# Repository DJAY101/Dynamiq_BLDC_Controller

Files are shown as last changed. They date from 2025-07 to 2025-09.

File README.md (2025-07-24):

# A simple Brushless Motor Controller
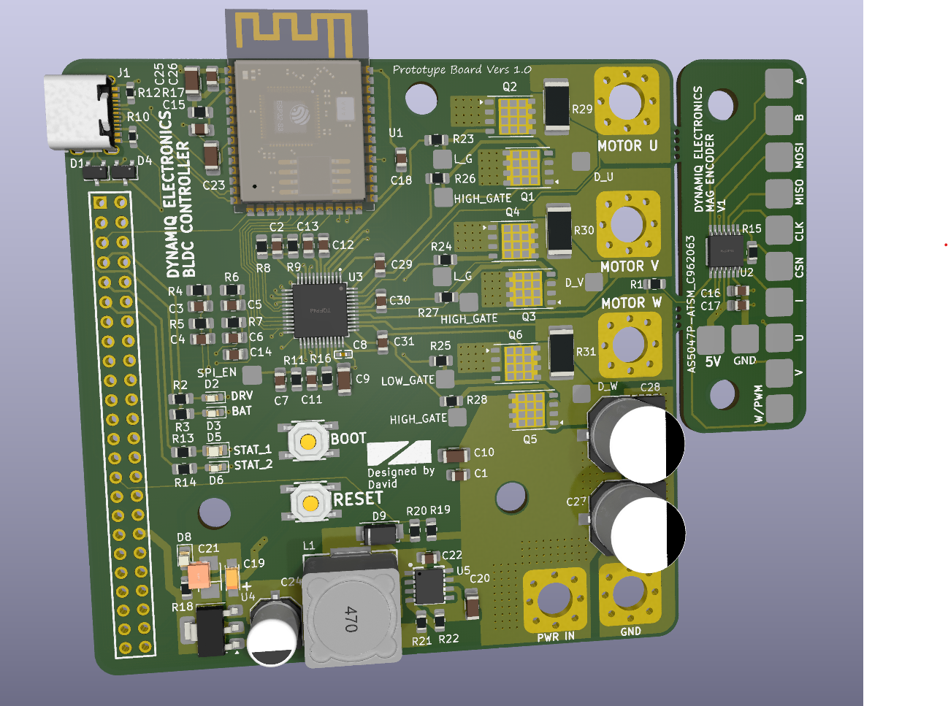
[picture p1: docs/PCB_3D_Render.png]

I'm currently on the journey of creating a simple cost effective controller that
will eventually be sold to the masses to remove the high barrier to entry into using high performing brushless motor actuators.

FRC Falcon 500 Motors inspired this project, since there are no suitable motor options at a suitable price that enables hobbyists to utilise these amazing pieces of technology. (Odrive being 200USD+)

# This project is still in its very early stages...
(Do note this is actually my very second PCB designed, so I lack a lot of experience)

Version 1 of the PCB worked with the following code. However I ended up frying two of the boards during programming and tinkering with the board. I am currently working on a version 2 iteration of the PCB from the mistakes and lack of safety features in V1. 

(I actually got the motor to turn on the very first iteration of this board which is a massive win)

## Failures so far...
- Somehow killed the TMC6200 gate driver while I was tinkering with the code. it does not like being fed a PWM duty cycle of greater than 40%
- Magic smoke occured on my buck converter where 4s Lipo is converted to 5V. Still unsure what happened here, but I have a few hypothesis. Sketchy soldering on my ESP32 3.3v and ground pin causing a short. Or accidentally shorting the the SPI clock pin with ground while unplugging the jumpers.
- The board does heat up, perhaps 2oZ layers may be needed (opted out since it was expensive for iter1)
- Practically no protection circuitry at all, except for the built in ones in the gate driver

# Improvements Underway
The progress on the code is halted as I have no working boards anymore since I fried all 2 of them haha.
- Integrate reverse polarity protection with a MOSFET Diode*
- Remove the chunky header pin and replace it with smaller header pins that connect to encoders and etc
- Initial inrush current limit to stop the spark when I connect my lipo to the board
- Fuses... Fuses and more fuses
- Change my LDO to a newer IC for more efficiency
- Capacitors on the phase output?
- Current sensing was not tested before the boards fried themselves ( caps on current sens outputs for a better averages value?)

# Other Unstructured Yap
PCB was manufactured by JLPCB, assembly services was also opted, 5 boards were 10 bucks aud and assembly and parts for 2 board added $150 aud

Reddit also reviewd my board before I manufactured it heres the link to that discussion
https://www.reddit.com/r/PCB/comments/1lk1n3d/review_request_my_first_pcb_bldc_sinusoidal/

This man made coding this thing a lot easier. Just pass sine waves into the motor and itll turn. I reckon it was much more easier to implement than step control.
https://www.youtube.com/watch?v=zSdetJsSeNw&t

Cool channels
- https://www.youtube.com/watch?v=mbJOxqxLkLE
- https://www.youtube.com/watch?v=e0sQnVmE7DU

If you'd like to contact me for more information or collaboration on this project feel free to DM me on insta at DJAY10101, or if you prefer email its djay01602@gmail.com

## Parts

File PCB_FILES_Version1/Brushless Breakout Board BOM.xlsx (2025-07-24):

Comment | Designator | Footprint | JLCPCB Part #（optional）
N-MOSFETS | Q1, Q2, Q3, Q4, Q5, Q6 | PG-TDSON-8 | C3288901
Buttons | SW1, SW2 | SW-SMD_4P-L5.2-W5.2-P3.70-LS6.5 | C10852
Mosfet Driver | U3 | TQFP-48_L7.0-W7.0-P0.50-LS9.0-BL-EP | C465958
ESP-32 MCU | U1 | SMD,18x25.5mm | C2913199
Jumper Connector | H1 | HC-PM254-8.5H-2X24PZ | C27985239
Mag Encoder | U2 | TSSOP-14 | C962063
Buck Convert IC | U5 | ESOP-8_L4.9-W3.9-P1.27-LS6.0-TL-EP | C9864
LDO IC | U4 | SOT-223 | C347222
ESD Protect IC | D1, D4 | SOT-23-3_L3.0-W1.7-P0.95-LS2.9-BR | C32677
USB C | J1 | TYPE-C-31-M-12 | C165948
Green LED | D8 | D0805 | C2297
LED Resistor 150R | R18, R2, R3, R13, R14 | R0805 | C17471
Red LED | D2, D3, D6 | D0603 | C2286
Yellow LED | D5 | D0805 | C2296
USB Resistor 5.1K | R10, R12 | R0603 | C23186
10K | R1, R4, R5, R6, R7, R8, R9, R11, R15, R17, R19, R21 | R0805 | C17414
10mR Shun Resistor | R29, R30, R31 | R2512 | C241862
2.2R Gate Resistors | R23, R24, R25, R26, R27, R28 | R0805 | C17521
47R | R16 | R0805 | C17714
1K | R20 | R0805 | C17513
3.3K | R22 | R0805 | C26010
15uH Buck Conv Inductor | L1 | IND-SMD_L12.5-W12.5_RLF12545T | C40000
SS34 Diode | D9 | SMA(DO-214AC) | C8678
100nF 100V Caps | C1, C2, C3, C4, C5, C6, C7, C14, C15, C17, C18, C26 | C0805 | C28233
100nF 50V Caps | C9, C10 | C1206 | C24497
100nf 16V Caps | C8 | C0402 | C1525
22nF 100V | C11 | C0805 | C184772
10uF 50V Caps | C20, C25 | C1206 | C13585
2.2uF 50V Caps | C13 | C0805 | C377773
4.7uF 25V | C12 | C0805 | C1779
1uF 50V | C16 | C0805 | C28323
22uF 10V Tantalum | C21 | CASE-B-3528-21(mm) | C7198
10nF 50V | C22 | C0805 | C1710
100uF 6.3V | C23 | C1206 | C15008
470uF | C27, C28 | CAP-SMD_BD10.0-L10.3-W10.3-LS11.3-FD | C3351
470nF 50V | C29, C30, C31 | C0805 | C13967
10uF 16V Tantalum | C19 | CASE-A-3216-18(mm) | C7171
220 uF capacitor | C24 | CAP-SMD_BD6.3-L6.6-W6.6-FD | C3342

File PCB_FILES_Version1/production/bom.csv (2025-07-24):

Designator | Footprint | Quantity | Value | LCSC Part #
C1, C14, C2 | 0805 | 3 | 100nF
C10, C9 | 1206 | 2 | 100nF 50V
C11 | 0805 | 1 | 22nF 100V
C12 | 0805 | 1 | 4.7uF
C13 | 0805 | 1 | 2.2uF
C15, C17, C18, C26, C3, C4, C5, C6, C7 | 0805 | 9 | 0.1uF
C16 | 0805 | 1 | 1uF
C19 | CAP-SMD_L3.2-W1.6-RD-C7171 | 1 | 10uF - TAJA106K016RNJ | C7171
C20, C25 | 1206 | 2 | 10uF
C21 | CAP-SMD_L3.5-W2.8-R-RD | 1 | 22uF Tant TAJB226K010RNJ | C7198
C22 | 0805 | 1 | 0.01uF
C23 | 1206 | 1 | 100uF
C24 | CAP-SMD_BD6.3-L6.6-W6.6-FD | 1 | 220uF-C3342 | C3342
C27, C28 | CAP-SMD_BD10.0-L10.3-W10.3-LS11.3-FD | 2 | 470uF -C3351 | C3351
C29, C30, C31 | 0805 | 3 | 470nF 16V
C8 | C0402 | 1 | 100nF 16V
D1, D4 | SOT-23-3_L3.0-W1.7-P0.95-LS2.9-BR | 2 | PSM712-LF-T7 | C32677
D2 | 0603 | 1 | Fault_LED
D3 | 0603 | 1 | LIPO_ALERT
D5 | 0805 | 1 | STATUS_1_LED
D6 | 0603 | 1 | STATUS_2_LED
D8 | 0805 | 1 | LED
D9 | SMA_L4.3-W2.6-LS5.2-RD | 1 | SS34
GND | PWR_THRU_HOLE | 1 | BAT_GND
H1 | HDR-TH_48P-P2.54-V-F-R2-C24-S2.54 | 1 | HC-PM254-8.5H-2X24PZ | C27985239
J1 | USB-C_SMD-TYPE-C-31-M-12 | 1 | USB_C_Receptacle_USB2.0_16P
L1 | IND-SMD_L12.5-W12.5_RLF12545T | 1 | 15uH
MOTOR U | PWR_THRU_HOLE | 1 | Motor_Phase_U
MOTOR V | PWR_THRU_HOLE | 1 | Motor_Phase_V
MOTOR W | PWR_THRU_HOLE | 1 | Motor_Phase_W
PWR IN | PWR_THRU_HOLE | 1 | BAT_IN
Q1, Q2, Q3, Q4, Q5, Q6 | Infineon_PG-TDSON-8_6.15x5.15mm | 6 | N_FET_ISC0602NLS
R1, R11, R15, R17, R19, R21, R4, R5, R6, R7, R8, R9 | 0805 | 12 | 10K
R10, R12 | 0603 | 2 | 5.1K
R13, R14, R18, R2, R3 | 0805 | 5 | 150
R16 | 0805 | 1 | 47
R20 | 0805 | 1 | 1K
R22 | 0805 | 1 | 3.3K
R23, R24, R25, R26, R27, R28 | 0805 | 6 | 2.2
R29, R30, R31 | 2512 | 3 | 10mR
SW1, SW2 | SW-SMD_4P-L5.2-W5.2-P3.70-LS6.5 | 2 | SW_MEC_5E
TP1 | PAD_TP | 1 | SPI_EN
TP10 | Small_Pad_4mm | 1 | 5V_ENCODER
TP11 | Small_Pad_4mm | 1 | U_ENCODER
TP12 | Small_Pad_4mm | 1 | V_ENCODER
TP13 | Small_Pad_4mm | 1 | W/PWM_ENCODER
TP19, TP20 | PAD_TP | 2 | L_G
TP2 | Small_Pad_4mm | 1 | CSN_ENCODER
TP21 | PAD_TP | 1 | LOW_GATE
TP22, TP23, TP24 | PAD_TP | 3 | HIGH_GATE
TP25 | PAD_TP | 1 | D_U
TP26 | PAD_TP | 1 | D_V
TP27 | PAD_TP | 1 | D_W
TP3 | Small_Pad_4mm | 1 | CLK_ENCODER
TP4 | Small_Pad_4mm | 1 | MISO_ENCODER
TP5 | Small_Pad_4mm | 1 | MOSI_ENCODER
TP6 | Small_Pad_4mm | 1 | GND_ENCODER
TP7 | Small_Pad_4mm | 1 | B_ENCODER
TP8 | Small_Pad_4mm | 1 | A_ENCODER
TP9 | Small_Pad_4mm | 1 | I_ENCODER
U1 | ESP32-S3-WROOM-1 | 1 | ESP32-S3-WROOM-1
U2 | TSSOP-14_L5.0-W4.4-P0.65-LS6.4-BL | 1 | AS5047P-ATSM_C962063 | C962063
U3 | TQFP-48_L7.0-W7.0-P0.50-LS9.0-BL-EP | 1 | TMC6200-TA-T | C465958
U4 | SOT-223-3_TabPin2 | 1 | AMS1117-3.3
U5 | ESOP-8_L4.9-W3.9-P1.27-LS6.0-TL-EP | 1 | TPS5430DDAR | C9864

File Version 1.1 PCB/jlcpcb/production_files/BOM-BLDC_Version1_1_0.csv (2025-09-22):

Comment | Designator | Footprint | LCSC | Quantity
SW_MEC_5E | SW1,SW2 | SW-SMD_4P-L5.2-W5.2-P3.70-LS6.5 | C10852 | 2
SM06B-GHS-TB(LF)(SN) | CN3 | CONN-TH_SM06B-GHS-TB-LF-SN | C133065 | 1
470nF 16V | C13,C14,C29 | C_0805_2012Metric_Pad1.18x1.45mm_HandSolder | C13967 | 3
100uF | C6,C9 | C_0805_2012Metric_Pad1.18x1.45mm_HandSolder | C141660 | 2
10uF | C1,C3,C7 | C_0805_2012Metric_Pad1.18x1.45mm_HandSolder | C15850 | 3
USB_C_Receptacle_USB2.0_14P | J1 | USB-C_SMD-TYPE-C-31-M-12 | C165948 | 1
0.01uF | C8 | C_0805_2012Metric_Pad1.18x1.45mm_HandSolder | C1710 | 1
10K | R10,R17,R19,R20,R21,R22,R24,R25,R27,R5,R8 | R_0805_2012Metric_Pad1.20x1.40mm_HandSolder | C17414 | 11
150 | R1,R2,R3,R4,R7 | R_0805_2012Metric_Pad1.20x1.40mm_HandSolder | C17471 | 5
1K | R6 | R_0805_2012Metric_Pad1.20x1.40mm_HandSolder | C17513 | 1
2.2 | R12,R13,R15,R16,R23,R26 | R_0805_2012Metric_Pad1.20x1.40mm_HandSolder | C17521 | 6
47 | R28 | R_0805_2012Metric_Pad1.20x1.40mm_HandSolder | C17714 | 1
4.7uF | C20,C4,C5 | C_0805_2012Metric_Pad1.18x1.45mm_HandSolder | C1779 | 3
LED | D1,D2 | LED_0603_1608Metric_Pad1.05x0.95mm_HandSolder | C2286 | 2
LED | D3 | LED_0805_2012Metric_Pad1.15x1.40mm_HandSolder | C2296 | 1
LED | D4,D6 | LED_0805_2012Metric_Pad1.15x1.40mm_HandSolder | C2297 | 2
3.3K | R11,R9 | R_0805_2012Metric_Pad1.20x1.40mm_HandSolder | C26010 | 2
0.1uF | C15,C17,C18,C2,C22,C23,C25,C26,C27 | C_0805_2012Metric_Pad1.18x1.45mm_HandSolder | C28233 | 9
2.2uF | C21 | C_0805_2012Metric_Pad1.18x1.45mm_HandSolder | C377773 | 1
DB910-7.62-3P | CN1 | CONN-TH_3P-P7.62_DB910-7.62-3P | C395877 | 1
SRV05-4-HXY | U10,U11,U13,U14 | SOT-23-6_L2.9-W1.6-P0.95-LS2.8-BR | C4748793 | 4
SM03B-GHS-TB(LF)(SN) | CN4 | CONN-TH_SM03B-GHS-TB-LF-SN | C514175 | 1
TestPoint | TP14,TP15,TP16,TP19,TP2,TP22,TP25,TP3,TP4,TP5,TP6,TP7 | SMD_RH-5015 | C5199798 | 12
22nF 100V | C28 | C_0805_2012Metric_Pad1.18x1.45mm_HandSolder | C61998 | 1
USBLC6-2SC6 | D9 | SOT-23-6_L2.9-W1.6-P0.95-LS2.8-BL | C7519 | 1
TPS5430DDAR | U4 | ESOP-8_L4.9-W3.9-P1.27-LS6.0-TL-EP | C9864 | 1
XT60PW-M | CN2 | CONN-TH_XT60PW-M | C98732 | 1

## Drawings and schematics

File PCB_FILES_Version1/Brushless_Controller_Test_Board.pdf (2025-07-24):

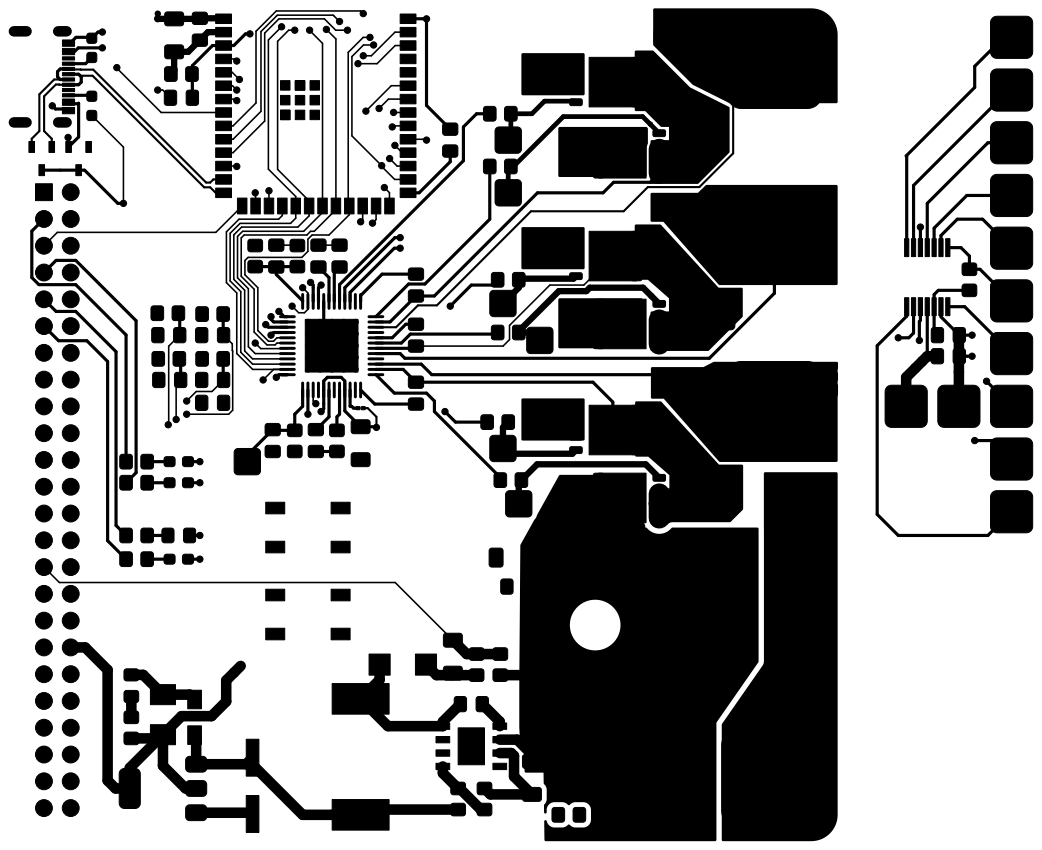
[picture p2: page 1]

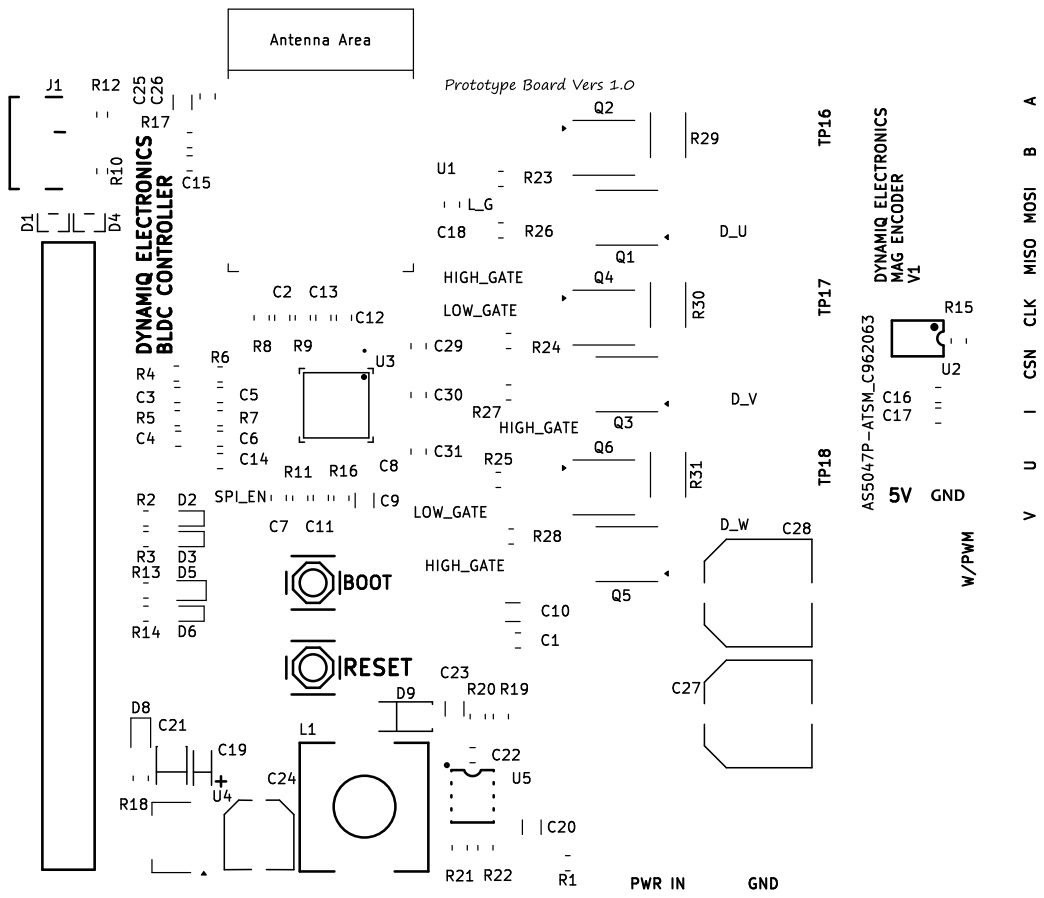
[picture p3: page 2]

B DYNAMIQ ELECTRONICS MAG ENCODER V1 CSN W/PWM

I DYNAMIQ ELECTRONICS BLDC CONTROLLER

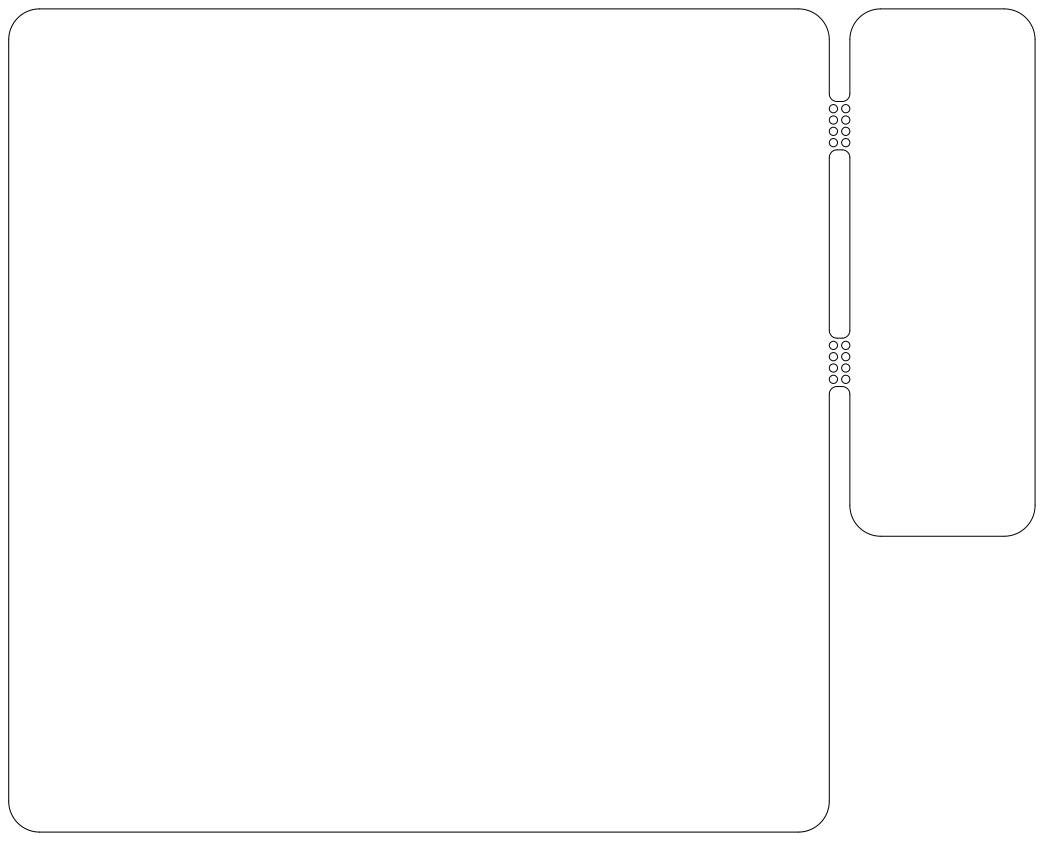
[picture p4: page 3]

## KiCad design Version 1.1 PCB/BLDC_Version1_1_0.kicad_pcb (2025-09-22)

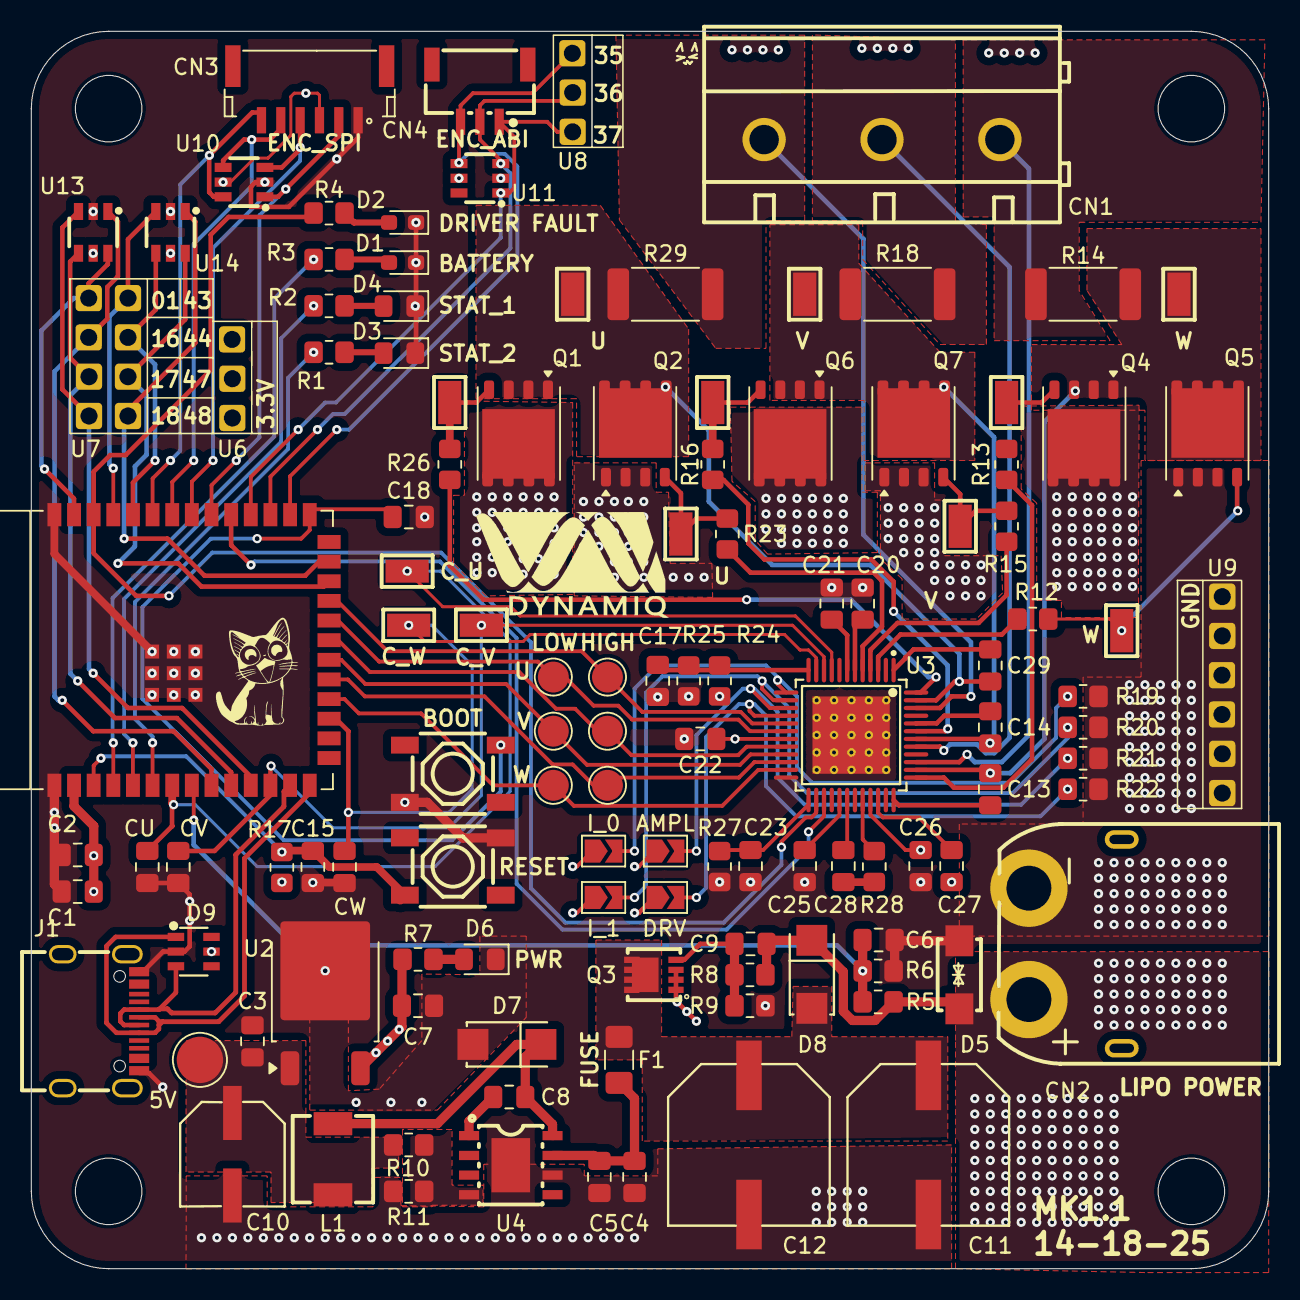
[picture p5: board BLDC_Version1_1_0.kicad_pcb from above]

Board: 4 copper layers, 80.0 x 80.0 mm, 118 parts (0 on the bottom side), 82 nets.

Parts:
5V: TestPoint; TestPoint_Pad_D3.0mm
AMPL: SolderJumper_2_Open; SolderJumper-2_P1.3mm_Open_TrianglePad1.0x1.5mm
C1, C3, C7: 10uF; C_0805_2012Metric_Pad1.18x1.45mm_HandSolder
C2, C15, C17, C18, C22, C23: 0.1uF; C_0805_2012Metric_Pad1.18x1.45mm_HandSolder
C4, C5, C20: 4.7uF; C_0805_2012Metric_Pad1.18x1.45mm_HandSolder
C6, C9: 100uF; C_0805_2012Metric_Pad1.18x1.45mm_HandSolder
C8: 0.01uF; C_0805_2012Metric_Pad1.18x1.45mm_HandSolder
C10: 220uF; CAP-SMD_BD6.3-L6.6-W6.6-FD
C11, C12: RVT1E471M1010-C3351; CAP-SMD_BD10.0-L10.3-W10.3-LS11.0-FD
C13, C14, C29: 470nF 16V; C_0805_2012Metric_Pad1.18x1.45mm_HandSolder
C21: 2.2uF; C_0805_2012Metric_Pad1.18x1.45mm_HandSolder
C25, C26: 0.1uF 50V; C_0805_2012Metric_Pad1.18x1.45mm_HandSolder
C27: 100nF 16V; C_0805_2012Metric_Pad1.18x1.45mm_HandSolder
C28: 22nF 100V; C_0805_2012Metric_Pad1.18x1.45mm_HandSolder
CN1: DB910-7.62-3P; CONN-TH_3P-P7.62_DB910-7.62-3P
CN2: XT60PW-M; CONN-TH_XT60PW-M
CN3: SM06B-GHS-TB(LF)(SN); CONN-TH_SM06B-GHS-TB-LF-SN
CN4: SM03B-GHS-TB(LF)(SN); CONN-TH_SM03B-GHS-TB-LF-SN
CU: C; C_0805_2012Metric_Pad1.18x1.45mm_HandSolder
CV: C; C_0805_2012Metric_Pad1.18x1.45mm_HandSolder
CW: C; C_0805_2012Metric_Pad1.18x1.45mm_HandSolder
D1, D2: LED; LED_0603_1608Metric_Pad1.05x0.95mm_HandSolder
D3, D4, D6: LED; LED_0805_2012Metric_Pad1.15x1.40mm_HandSolder
D5: SMAJ18CA_C908822; SMA_L4.4-W2.8-LS5.1-BI
D7, D8: B340A-E3/61T; SMA_L4.3-W2.6-LS5.2-RD
D9: USBLC6-2SC6; SOT-23-6_L2.9-W1.6-P0.95-LS2.8-BL
DRV: SolderJumper_2_Open; SolderJumper-2_P1.3mm_Open_TrianglePad1.0x1.5mm
F1: 1A Fuse; Fuse_1206_3216Metric_Pad1.42x1.75mm_HandSolder
I_0, I_1: SolderJumper_2_Open; SolderJumper-2_P1.3mm_Open_TrianglePad1.0x1.5mm
J1: USB_C_Receptacle_USB2.0_14P; USB-C_SMD-TYPE-C-31-M-12
L1: 22uH; IND-SMD_L5.5-W5.2
Q1, Q2, Q4, Q5, Q6, Q7: N_FET_ISC0602NLS; Infineon_PG-TDSON-8_6.15x5.15mm
Q3: SI7129DN-T1-GE3; POWERPAK-1212-8_L3.3-W3.3-P0.65-BL-EP
R1, R2, R3, R4, R7: 150; R_0805_2012Metric_Pad1.20x1.40mm_HandSolder
R5, R8, R10, R17, R19, R20, R21, R22, R24, R25, R27: 10K; R_0805_2012Metric_Pad1.20x1.40mm_HandSolder
R6: 1K; R_0805_2012Metric_Pad1.20x1.40mm_HandSolder
R9, R11: 3.3K; R_0805_2012Metric_Pad1.20x1.40mm_HandSolder
R12, R13, R15, R16, R23, R26: 2.2; R_0805_2012Metric_Pad1.20x1.40mm_HandSolder
R14, R18, R29: 10mR; R_2512_6332Metric_Pad1.40x3.35mm_HandSolder
R28: 47; R_0805_2012Metric_Pad1.20x1.40mm_HandSolder
SW1, SW2: SW_MEC_5E; SW-SMD_4P-L5.2-W5.2-P3.70-LS6.5
TP2, TP5, TP19: LOW_GATE; SMD_RH-5015
TP3, TP6, TP22: HIGH_GATE; SMD_RH-5015
TP4, TP7, TP25: OUTPUT_POINT; SMD_RH-5015
TP8, TP9, TP10, TP11, TP12, TP13: TestPoint; TestPoint_Pad_D2.0mm
TP14, TP15, TP16: TestPoint; SMD_RH-5015
U1: ESP32-S3-WROOM-1
U2: AP7363-33D-13; TO-252-2
U3: TMC6200-TA-T; TQFP-48_L7.0-W7.0-P0.50-LS9.0-BL-EP
U4: TPS5430DDAR; ESOP-8_L4.9-W3.9-P1.27-LS6.0-TL-EP
U6, U8: 1x3 Male Headers
U7: 8x Male Headers; 2x4 Male Headers
U9: Male Headers; 1x6 Male Headers
U10, U11, U13, U14: SRV05-4-HXY; SOT-23-6_L2.9-W1.6-P0.95-LS2.8-BR

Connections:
3.3V_BUS: AMPL.1 (A), C1.1, C2.1, C7.1, C22.1, CN3.3, D9.5, DRV.1 (A), I_0.1 (A), I_1.1 (A), R7.1, R17.1, R24.1, U1.2 (3V3), U2.3 (OUT), U3.19 (VCC_IO), U6.1, U6.2, U6.3, U10.5 (VBUS), U11.5 (VBUS), U13.5 (VBUS), U14.5 (VBUS)
5V_BUS: 5V.1, C3.1, C10.1, L1.2, R10.1, U2.1 (IN)
16.8V_BUS: C9.2, C25.1, C26.1, C27.1, CN2.2 (+), D5.2, D8.1 (K), Q1.5 (D), Q3.1 (S), Q3.2 (S), Q3.3 (S), Q4.5 (D), Q6.5 (D), R5.1, R8.1, U3.29 (VSA), U3.33 (VS)
/Power Management/SOFTSTART_PWR_IN: C11.1, C12.1, D8.2 (A), F1.1, Q3.5 (D), Q3.6 (D), Q3.7 (D), Q3.8 (D)
BOOT: C18.1, SW2.3 (K), U1.27 (GPIO0/BOOT)
CHARGE_CAPACITOR_INPUT: R28.2, U3.32 (CPI)
CHARGE_CAPACITOR_OUTPUT: C28.1, U3.30 (CPO)
CURRENT_SENS_VOFS: C17.1, R24.2, R25.1, U3.12 (VOFS/TEST)
CURRENT_U: CU.1, TP14.1, U1.7 (GPIO7/TOUCH7/ADC1_CH6), U3.9 (CURU)
CURRENT_V: CV.1, TP15.1, U1.12 (GPIO8/TOUCH8/ADC1_CH7/SUBSPICS1), U3.10 (CURV)
CURRENT_W: CW.1, TP16.1, U1.17 (GPIO9/TOUCH9/ADC1_CH8/FSPIHD/SUBSPIHD), U3.11 (CURW)
DRIVER_CSN/IDRV0: I_0.2 (B), R19.1, U3.13 (CSN_IDRV0)
DRIVER_SCK/IDRV1: I_1.2 (B), R20.1, U3.14 (SCK_IDRV1)
DRIVER_SDI/AMPL: AMPL.2 (B), R21.1, U3.15 (SDI_AMPLx10)
DRIVER_SDO/SINGLE: DRV.2 (B), R22.1, U3.16 (SDO_SINGLE)
DRIVER_U: C29.2, Q1.1 (S), Q1.2 (S), Q1.3 (S), Q2.5 (D), R29.1, TP25.1, U3.47 (U)
DRIVER_V: C14.2, Q6.1 (S), Q6.2 (S), Q6.3 (S), Q7.5 (D), R18.1, TP7.1, U3.42 (V)
DRIVER_W: C13.2, Q4.1 (S), Q4.2 (S), Q4.3 (S), Q5.5 (D), R14.1, TP4.1, U3.38 (W)
DRV_ENABLE: U1.31 (GPIO38/FSPIWP/SUBSPIWP), U3.27 (DEV_EN)
DRV_FAULT: R4.1, U1.38 (GPIO2/TOUCH2/ADC1_CH1), U3.26 (FAULT)
EN: C15.1, R17.2, SW1.3 (K), U1.3 (EN)
ENCODER_CLK: CN3.2, U1.32 (MTCK/GPIO39/CLK_OUT3/SUBSPICS1), U10.1
ENCODER_CSN: CN3.6, U1.35 (MTMS/GPIO42), U10.6
ENCODER_MISO: CN3.4, U1.33 (MTDO/GPIO40/CLK_OUT2), U10.3
ENCODER_MOSI: CN3.5, U1.34 (MTDI/GPIO41/CLK_OUT1), U10.4
GND: C1.2, C2.2, C3.2, C4.2, C5.2, C6.2, C7.2, C10.2, C11.2, C12.2, C15.2, C17.2, C18.2, C20.2, C21.2, C22.2, C23.2, C25.2, C26.2, CN2.1 (-), CN3.1, CU.2, CV.2, CW.2, D1.1 (K), D2.1 (K), D3.1 (K), D4.1 (K), D5.1, D6.1 (K), D7.2 (A), D9.2, J1.A1 (GND), J1.A12 (GND), J1.B1 (GND), J1.B12 (GND), Q2.1 (S), Q2.2 (S), Q2.3 (S), Q5.1 (S), Q5.2 (S), Q5.3 (S), Q7.1 (S), Q7.2 (S), Q7.3 (S), R6.2, R9.2, R11.2, R19.2, R20.2, R21.2, R22.2, R25.2, R27.2, SW1.2, SW2.2, U1.1 (GND), U1.40 (GND), U1.41 (GND), U2.2 (GND), U3.8 (GNDA), U3.24 (CLK), U3.49 (EP), U4.6 (GND), U4.9 (PowerPAD), U9.1, U9.2, U9.3, U9.4, U9.5, U9.6, U10.2 (GND), U11.2 (GND), U13.2 (GND), U14.2 (GND)
GPIO01: U1.39 (GPIO1/TOUCH1/ADC1_CH0), U7.1, U13.6
GPIO16: U1.9 (GPIO16/U0CTS/ADC2_CH5/XTAL_32K_N), U7.2, U13.1
GPIO17: U1.10 (GPIO17/U1TXD/ADC2_CH6), U7.3, U13.4
GPIO18: U1.11 (GPIO18/U1RXD/ADC2_CH7/CLK_OUT3), U7.4, U13.3
GPIO35: CN4.3, U1.28 (SPIIO6/GPIO35/FSPID/SUBSPID), U8.3, U11.4
GPIO36: CN4.2, U1.29 (SPIIO7/GPIO36/FSPICLK/SUBSPICLK), U8.2, U11.3
GPIO37: CN4.1, U1.30 (SPIDQS/GPIO37/FSPIQ/SUBSPIQ), U8.1, U11.1
GPIO43: U1.37 (U0TXD/GPIO43/CLK_OUT1), U7.5, U14.3
GPIO44: U1.36 (U0RXD/GPIO44/CLK_OUT2), U7.6, U14.4
GPIO47: U1.24 (GPIO47/SPICLK_P/SUBSPICLK_P_DIFF), U7.7, U14.6
GPIO48: U1.25 (GPIO48/SPICLK_N/SUBSPICLK_N_DIFF), U7.8, U14.1
LIPO_FAULT: R3.1, U1.4 (GPIO4/TOUCH4/ADC1_CH3)
LIPO_VOLT_SENS: C6.1, R5.2, R6.1, U1.8 (GPIO15/U0RTS/ADC2_CH4/XTAL_32K_P)
unnamed: C28.2, R28.1
unnamed: D1.2 (A), R3.2
unnamed: D2.2 (A), R4.2
unnamed: D3.2 (A), R1.2
unnamed: D4.2 (A), R2.2
unnamed: D6.2 (A), R7.2
unnamed: C8.2, D7.1 (K), L1.1, U4.8 (PH)
unnamed: Q1.4 (G), R26.2, TP22.1
unnamed: Q2.4 (G), R23.2, TP19.1
unnamed: C9.1, Q3.4 (G), R8.2, R9.1
unnamed: Q4.4 (G), R13.2, TP3.1
unnamed: Q5.4 (G), R12.2, TP2.1
unnamed: Q6.4 (G), R16.2, TP6.1
unnamed: Q7.4 (G), R15.2, TP5.1
unnamed: C21.1, U3.7 (5VOUT)
unnamed: C20.1, U3.6 (12VOUT)
unnamed: C23.1, R27.1, U3.25 (SPE)
unnamed: C8.1, U4.1 (BOOT)
unnamed: C4.1, C5.1, F1.2, U4.7 (VIN)
unnamed: R10.2, R11.1, U4.4 (VSENSE)
STATUS_1: R2.1, U1.5 (GPIO5/TOUCH5/ADC1_CH4)
STATUS_2: R1.1, U1.6 (GPIO6/TOUCH6/ADC1_CH5)
USB_D +: D9.1, J1.A6 (D+), J1.B6 (D+), U1.14 (GPIO20/U1CTS/ADC2_CH9/CLK_OUT1/USB_D+)
USB_D -: D9.3, J1.A7 (D-), J1.B7 (D-), U1.13 (GPIO19/U1RTS/ADC2_CH8/CLK_OUT2/USB_D-)
U_BOOTSTRAP: C29.1, U3.1 (CU)
U_HIGHSIDE: TP8.1, U1.23 (GPIO21), U3.17 (UH)
U_HIGHSIDE_GATE: R26.1, U3.48 (HSU)
U_LOWSIDE: TP9.1, U1.22 (GPIO14/TOUCH14/ADC2_CH3/FSPIWP/FSPIDQS/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), U3.18 (UL)
U_LOWSIDE_GATE: R23.1, U3.5 (LSU)
U_SENSE: CN1.3, R29.2, U3.46 (USENSE)
VOLTAGE_CHARGE_PUMP: C27.2, U3.34 (VCP)
V_BOOTSTRAP: C14.1, U3.44 (CV)
V_HIGHSIDE: TP10.1, U1.21 (GPIO13/TOUCH13/ADC2_CH2/FSPIQ/FSPIIO7/S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), U3.20 (VH)
V_HIGHSIDE_GATE: R16.1, U3.43 (HSV)
V_LOWSIDE: TP11.1, U1.20 (GPIO12/TOUCH12/ADC2_CH1/FSPICLK/FSPIIO6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), U3.21 (VL)
V_LOWSIDE_GATE: R15.1, U3.4 (LSV)
V_SENSE: CN1.2, R18.2, U3.41 (VSENSE)
W_BOOTSTRAP: C13.1, U3.36 (CW)
W_HIGHSIDE: TP12.1, U1.19 (GPIO11/TOUCH11/ADC2_CH0/FSPID/FSPIIO5/S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), U3.22 (WH)
W_HIGHSIDE_GATE: R13.1, U3.37 (HSW)
W_LOWSIDE: TP13.1, U1.18 (GPIO10/TOUCH10/ADC1_CH9/FSPICS0/FSPIIO4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), U3.23 (WL)
W_LOWSIDE_GATE: R12.1, U3.3 (LSW)
W_SENSE: CN1.1, R14.2, U3.39 (WSENSE)

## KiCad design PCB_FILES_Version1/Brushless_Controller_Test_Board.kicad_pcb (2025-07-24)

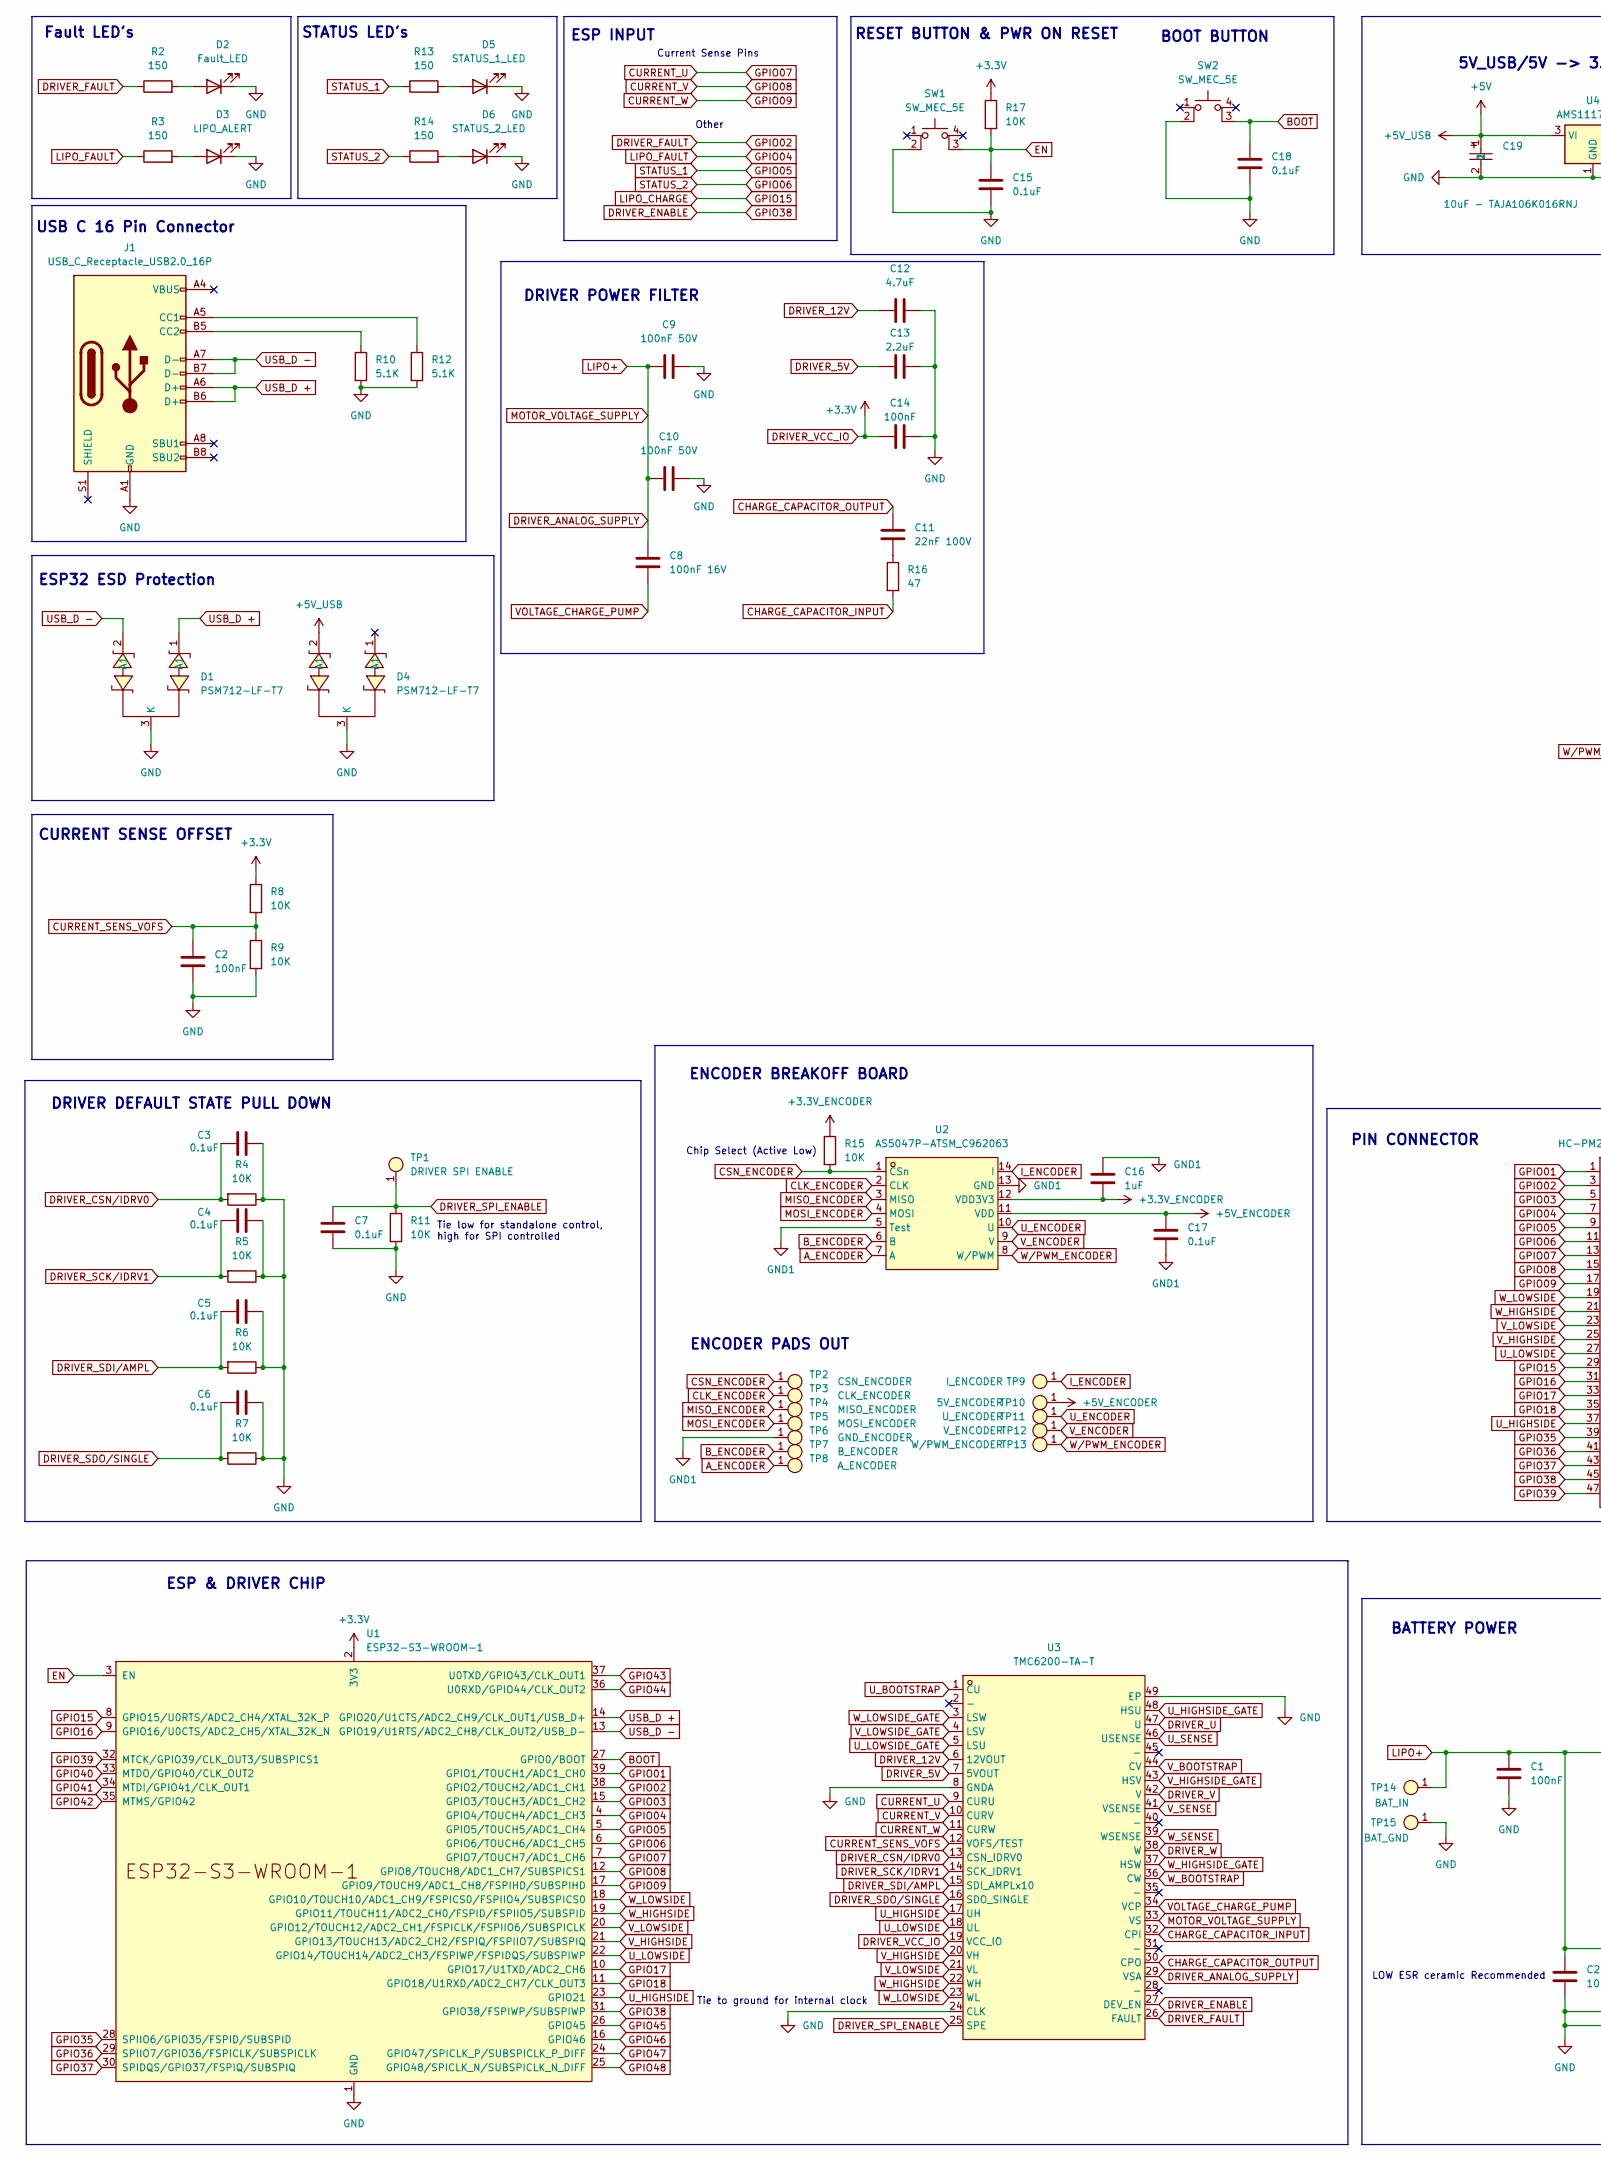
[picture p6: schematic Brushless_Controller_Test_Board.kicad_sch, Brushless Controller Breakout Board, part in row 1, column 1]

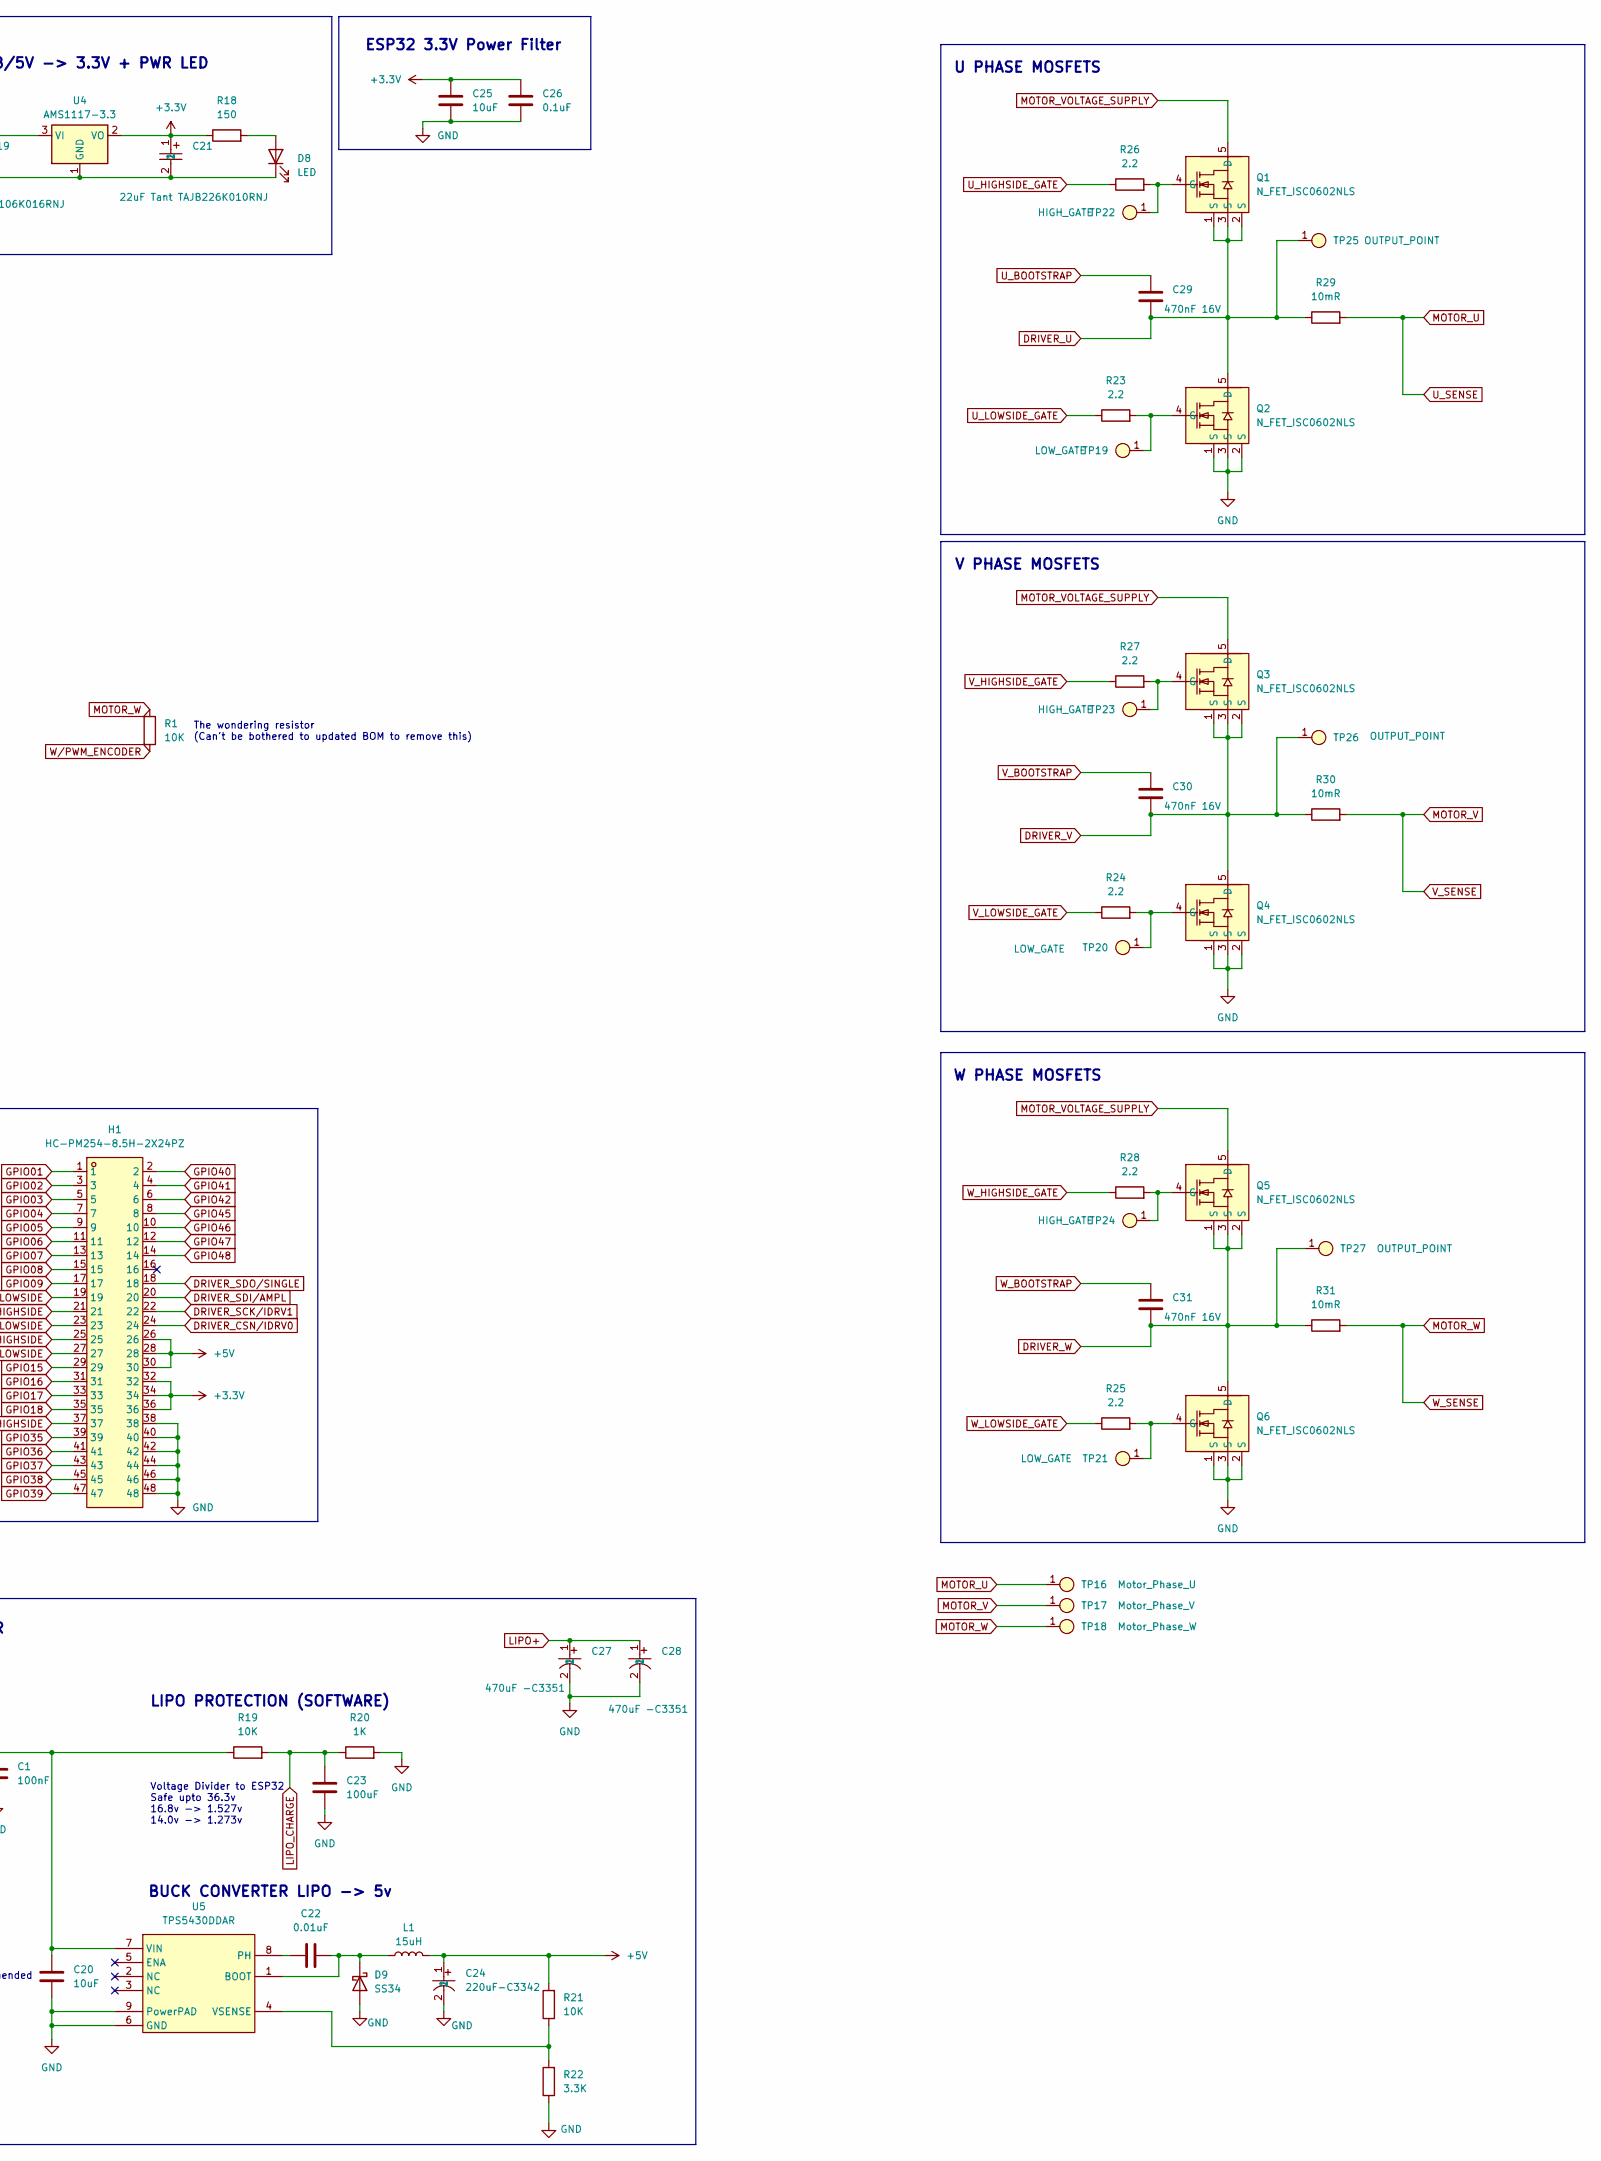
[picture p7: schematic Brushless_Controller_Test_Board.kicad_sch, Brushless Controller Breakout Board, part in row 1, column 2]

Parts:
C1, C2, C14: 100nF; C_0805_2012Metric_Pad1.18x1.45mm_HandSolder
C3, C4, C5, C6, C7, C15, C17, C18, C26: 0.1uF; C_0805_2012Metric_Pad1.18x1.45mm_HandSolder
C8: 100nF 16V; C_01005_0402Metric_Pad0.57x0.30mm_HandSolder
C9, C10: 100nF 50V; C_1206_3216Metric_Pad1.33x1.80mm_HandSolder
C11: 22nF 100V; C_0805_2012Metric_Pad1.18x1.45mm_HandSolder
C12: 4.7uF; C_0805_2012Metric_Pad1.18x1.45mm_HandSolder
C13: 2.2uF; C_0805_2012Metric_Pad1.18x1.45mm_HandSolder
C16: 1uF; C_0805_2012Metric_Pad1.18x1.45mm_HandSolder
C19: 10uF - TAJA106K016RNJ; CAP-SMD_L3.2-W1.6-RD-C7171; LCSC Part C7171
C20, C25: 10uF; C_1206_3216Metric_Pad1.33x1.80mm_HandSolder
C21: 22uF Tant TAJB226K010RNJ; CAP-SMD_L3.5-W2.8-R-RD; LCSC Part C7198
C22: 0.01uF; C_0805_2012Metric_Pad1.18x1.45mm_HandSolder
C23: 100uF; C_1206_3216Metric_Pad1.33x1.80mm_HandSolder
C24: 220uF-C3342; CAP-SMD_BD6.3-L6.6-W6.6-FD; LCSC Part C3342
C27, C28: 470uF -C3351; CAP-SMD_BD10.0-L10.3-W10.3-LS11.3-FD; LCSC Part C3351
C29, C30, C31: 470nF 16V; C_0805_2012Metric_Pad1.18x1.45mm_HandSolder
D1, D4: PSM712-LF-T7; SOT-23-3_L3.0-W1.7-P0.95-LS2.9-BR; LCSC Part C32677
D2: Fault_LED; LED_0603_1608Metric_Pad1.05x0.95mm_HandSolder
D3: LIPO_ALERT; LED_0603_1608Metric_Pad1.05x0.95mm_HandSolder
D5: STATUS_1_LED; LED_0805_2012Metric_Pad1.15x1.40mm_HandSolder
D6: STATUS_2_LED; LED_0603_1608Metric_Pad1.05x0.95mm_HandSolder
D8: LED; LED_0805_2012Metric_Pad1.15x1.40mm_HandSolder
D9: SS34; SMA_L4.3-W2.6-LS5.2-RD
H1: HC-PM254-8.5H-2X24PZ; HDR-TH_48P-P2.54-V-F-R2-C24-S2.54; LCSC Part C27985239
J1: USB_C_Receptacle_USB2.0_16P; USB-C_SMD-TYPE-C-31-M-12
L1: 15uH; IND-SMD_L12.5-W12.5_RLF12545T
Q1, Q2, Q3, Q4, Q5, Q6: N_FET_ISC0602NLS; Infineon_PG-TDSON-8_6.15x5.15mm
R1, R4, R5, R6, R7, R8, R9, R11, R15, R17, R19, R21: 10K; R_0805_2012Metric_Pad1.20x1.40mm_HandSolder
R2, R3, R13, R14, R18: 150; R_0805_2012Metric_Pad1.20x1.40mm_HandSolder
R10, R12: 5.1K; R_0603_1608Metric_Pad0.98x0.95mm_HandSolder
R16: 47; R_0805_2012Metric_Pad1.20x1.40mm_HandSolder
R20: 1K; R_0805_2012Metric_Pad1.20x1.40mm_HandSolder
R22: 3.3K; R_0805_2012Metric_Pad1.20x1.40mm_HandSolder
R23, R24, R25, R26, R27, R28: 2.2; R_0805_2012Metric_Pad1.20x1.40mm_HandSolder
R29, R30, R31: 10mR; R_2512_6332Metric_Pad1.40x3.35mm_HandSolder
SW1, SW2: SW_MEC_5E; SW-SMD_4P-L5.2-W5.2-P3.70-LS6.5
TP1: DRIVER SPI ENABLE; PAD_TP
TP2: CSN_ENCODER; Small_Pad_4mm
TP3: CLK_ENCODER; Small_Pad_4mm
TP4: MISO_ENCODER; Small_Pad_4mm
TP5: MOSI_ENCODER; Small_Pad_4mm
TP6: GND_ENCODER; Small_Pad_4mm
TP7: B_ENCODER; Small_Pad_4mm
TP8: A_ENCODER; Small_Pad_4mm
TP9: I_ENCODER; Small_Pad_4mm
TP10: 5V_ENCODER; Small_Pad_4mm
TP11: U_ENCODER; Small_Pad_4mm
TP12: V_ENCODER; Small_Pad_4mm
TP13: W/PWM_ENCODER; Small_Pad_4mm
TP14: BAT_IN; Large_Pad_9mm
TP15: BAT_GND; Large_Pad_9mm
TP16: Motor_Phase_U; PWR_THRU_HOLE
TP17: Motor_Phase_V; PWR_THRU_HOLE
TP18: Motor_Phase_W; PWR_THRU_HOLE
TP19, TP20, TP21: LOW_GATE; PAD_TP
TP22, TP23, TP24: HIGH_GATE; PAD_TP
TP25, TP26, TP27: OUTPUT_POINT; PAD_TP
U1: ESP32-S3-WROOM-1
U2: AS5047P-ATSM_C962063; TSSOP-14_L5.0-W4.4-P0.65-LS6.4-BL; LCSC Part C962063
U3: TMC6200-TA-T; TQFP-48_L7.0-W7.0-P0.50-LS9.0-BL-EP; LCSC Part C465958
U4: AMS1117-3.3; SOT-223-3_TabPin2
U5: TPS5430DDAR; ESOP-8_L4.9-W3.9-P1.27-LS6.0-TL-EP; LCSC Part C9864

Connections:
+3.3V_ENCODER: C16.2, R15.1, U2.12 (VDD3V3)
+5V: C19.1, C24.1, D4.2 (A1), H1.26, H1.28, H1.30, L1.2, R21.2, U4.3 (VI)
+5V_ENCODER: C17.1, TP10.1, U2.11 (VDD)
A_ENCODER: TP8.1, U2.7 (A)
BOOT: C18.1, SW2.3 (K), U1.27 (GPIO0/BOOT)
B_ENCODER: TP7.1, U2.6 (B)
CHARGE_CAPACITOR_INPUT: R16.2, U3.32 (CPI)
CHARGE_CAPACITOR_OUTPUT: C11.2, U3.30 (CPO)
CLK_ENCODER: TP3.1, U2.2 (CLK)
CSN_ENCODER: R15.2, TP2.1, U2.1 (CSn)
CURRENT_SENS_VOFS: C2.1, R8.2, R9.1, U3.12 (VOFS/TEST)
CURRENT_U: H1.13, U1.7 (GPIO7/TOUCH7/ADC1_CH6), U3.9 (CURU)
CURRENT_V: H1.15, U1.12 (GPIO8/TOUCH8/ADC1_CH7/SUBSPICS1), U3.10 (CURV)
CURRENT_W: H1.17, U1.17 (GPIO9/TOUCH9/ADC1_CH8/FSPIHD/SUBSPIHD), U3.11 (CURW)
DRIVER_5V: C13.2, U3.7 (5VOUT)
DRIVER_12V: C12.2, U3.6 (12VOUT)
DRIVER_ANALOG_SUPPLY: C1.2, C8.1, C9.1, C10.1, C20.1, C27.1, C28.1, Q1.5 (D), Q3.5 (D), Q5.5 (D), R19.1, TP14.1, U3.29 (VSA), U3.33 (VS), U5.7 (VIN); also elsewhere on the board
DRIVER_CSN/IDRV0: C3.2, H1.24, R4.2, U3.13 (CSN_IDRV0)
DRIVER_ENABLE: H1.45, U1.31 (GPIO38/FSPIWP/SUBSPIWP), U3.27 (DEV_EN)
DRIVER_FAULT: H1.3, R2.1, U1.38 (GPIO2/TOUCH2/ADC1_CH1), U3.26 (FAULT)
DRIVER_SCK/IDRV1: C4.2, H1.22, R5.2, U3.14 (SCK_IDRV1)
DRIVER_SDI/AMPL: C5.2, H1.20, R6.2, U3.15 (SDI_AMPLx10)
DRIVER_SDO/SINGLE: C6.2, H1.18, R7.2, U3.16 (SDO_SINGLE)
DRIVER_SPI_ENABLE: C7.1, R11.2, TP1.1, U3.25 (SPE)
DRIVER_U: C29.2, Q1.1 (S), Q1.2 (S), Q1.3 (S), Q2.5 (D), R29.1, TP25.1, U3.47 (U)
DRIVER_V: C30.2, Q3.1 (S), Q3.2 (S), Q3.3 (S), Q4.5 (D), R30.1, TP26.1, U3.42 (V)
DRIVER_VCC_IO: C14.2, C21.1, C25.1, C26.1, H1.32, H1.34, H1.36, R8.1, R17.1, R18.1, U1.2 (3V3), U3.19 (VCC_IO), U4.2 (VO)
DRIVER_W: C31.2, Q5.1 (S), Q5.2 (S), Q5.3 (S), Q6.5 (D), R31.1, TP27.1, U3.38 (W)
EN: C15.1, R17.2, SW1.3 (K), U1.3 (EN)
GND: C1.1, C2.2, C3.1, C4.1, C5.1, C6.1, C7.2, C9.2, C10.2, C12.1, C13.1, C14.1, C15.2, C18.2, C19.2, C20.2, C21.2, C23.2, C24.2, C25.2, C26.2, C27.2, C28.2, D1.3 (K), D2.1 (K), D3.1 (K), D4.3 (K), D5.1 (K), D6.1 (K), D8.1 (K), D9.2 (A), H1.38, H1.40, H1.42, H1.44, H1.46, H1.48, J1.A1 (GND), J1.A12 (GND), J1.B1 (GND), J1.B12 (GND), Q2.1 (S), Q2.2 (S), Q2.3 (S), Q4.1 (S), Q4.2 (S), Q4.3 (S), Q6.1 (S), Q6.2 (S), Q6.3 (S), R4.1, R5.1, R6.1, R7.1, R9.2, R10.2, R11.1, R12.2, R20.2, R22.1, SW1.2, SW2.2, TP15.1, U1.1 (GND), U1.40 (GND), U1.41 (GND), U3.8 (GNDA), U3.24 (CLK), U3.49 (EP), U4.1 (GND), U5.6 (GND), U5.9 (PowerPAD); also elsewhere on the board
GND1: C16.1, C17.2, TP6.1, U2.5 (Test), U2.13 (GND)
GPIO01: H1.1, U1.39 (GPIO1/TOUCH1/ADC1_CH0)
GPIO03: H1.5, U1.15 (GPIO3/TOUCH3/ADC1_CH2)
GPIO04: H1.7, R3.1, U1.4 (GPIO4/TOUCH4/ADC1_CH3)
GPIO05: H1.9, R13.1, U1.5 (GPIO5/TOUCH5/ADC1_CH4)
GPIO06: H1.11, R14.1, U1.6 (GPIO6/TOUCH6/ADC1_CH5)
GPIO15: C23.1, H1.29, R19.2, R20.1, U1.8 (GPIO15/U0RTS/ADC2_CH4/XTAL_32K_P)
GPIO16: H1.31, U1.9 (GPIO16/U0CTS/ADC2_CH5/XTAL_32K_N)
GPIO17: H1.33, U1.10 (GPIO17/U1TXD/ADC2_CH6)
GPIO18: H1.35, U1.11 (GPIO18/U1RXD/ADC2_CH7/CLK_OUT3)
GPIO35: H1.39, U1.28 (SPIIO6/GPIO35/FSPID/SUBSPID)
GPIO36: H1.41, U1.29 (SPIIO7/GPIO36/FSPICLK/SUBSPICLK)
GPIO37: H1.43, U1.30 (SPIDQS/GPIO37/FSPIQ/SUBSPIQ)
GPIO39: H1.47, U1.32 (MTCK/GPIO39/CLK_OUT3/SUBSPICS1)
GPIO40: H1.2, U1.33 (MTDO/GPIO40/CLK_OUT2)
GPIO41: H1.4, U1.34 (MTDI/GPIO41/CLK_OUT1)
GPIO42: H1.6, U1.35 (MTMS/GPIO42)
GPIO43: U1.37 (U0TXD/GPIO43/CLK_OUT1)
GPIO44: U1.36 (U0RXD/GPIO44/CLK_OUT2)
GPIO45: H1.8, U1.26 (GPIO45)
GPIO46: H1.10, U1.16 (GPIO46)
GPIO47: H1.12, U1.24 (GPIO47/SPICLK_P/SUBSPICLK_P_DIFF)
GPIO48: H1.14, U1.25 (GPIO48/SPICLK_N/SUBSPICLK_N_DIFF)
I_ENCODER: TP9.1, U2.14 (I)
MISO_ENCODER: TP4.1, U2.3 (MISO)
MOSI_ENCODER: TP5.1, U2.4 (MOSI)
MOTOR_U: R29.2, TP16.1, U3.46 (USENSE); also elsewhere on the board
MOTOR_V: R30.2, TP17.1, U3.41 (VSENSE); also elsewhere on the board
MOTOR_W: R1.1, R31.2, TP18.1, U3.39 (WSENSE); also elsewhere on the board
unnamed: C11.1, R16.1
unnamed: D2.2 (A), R2.2
unnamed: D3.2 (A), R3.2
unnamed: D5.2 (A), R13.2
unnamed: D6.2 (A), R14.2
unnamed: D8.2 (A), R18.2
unnamed: C22.1, D9.1 (K), L1.1, U5.1 (BOOT)
unnamed: J1.A5 (CC1), R12.1
unnamed: J1.B5 (CC2), R10.1
unnamed: Q1.4 (G), R26.2, TP22.1
unnamed: Q2.4 (G), R23.2, TP19.1
unnamed: Q3.4 (G), R27.2, TP23.1
unnamed: Q4.4 (G), R24.2, TP20.1
unnamed: Q5.4 (G), R28.2, TP24.1
unnamed: Q6.4 (G), R25.2, TP21.1
unnamed: C22.2, U5.8 (PH)
unnamed: R21.1, R22.2, U5.4 (VSENSE)
USB_D +: D1.1 (A1), J1.A6 (D+), J1.B6 (D+), U1.14 (GPIO20/U1CTS/ADC2_CH9/CLK_OUT1/USB_D+)
USB_D -: D1.2 (A1), J1.A7 (D-), J1.B7 (D-), U1.13 (GPIO19/U1RTS/ADC2_CH8/CLK_OUT2/USB_D-)
U_BOOTSTRAP: C29.1, U3.1 (CU)
U_ENCODER: TP11.1, U2.10 (U)
U_HIGHSIDE: H1.37, U1.23 (GPIO21), U3.17 (UH)
U_HIGHSIDE_GATE: R26.1, U3.48 (HSU)
U_LOWSIDE: H1.27, U1.22 (GPIO14/TOUCH14/ADC2_CH3/FSPIWP/FSPIDQS/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), U3.18 (UL)
U_LOWSIDE_GATE: R23.1, U3.5 (LSU)
VOLTAGE_CHARGE_PUMP: C8.2, U3.34 (VCP)
V_BOOTSTRAP: C30.1, U3.44 (CV)
V_ENCODER: TP12.1, U2.9 (V)
V_HIGHSIDE: H1.25, U1.21 (GPIO13/TOUCH13/ADC2_CH2/FSPIQ/FSPIIO7/S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), U3.20 (VH)
V_HIGHSIDE_GATE: R27.1, U3.43 (HSV)
V_LOWSIDE: H1.23, U1.20 (GPIO12/TOUCH12/ADC2_CH1/FSPICLK/FSPIIO6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), U3.21 (VL)
V_LOWSIDE_GATE: R24.1, U3.4 (LSV)
W_BOOTSTRAP: C31.1, U3.36 (CW)
W_HIGHSIDE: H1.21, U1.19 (GPIO11/TOUCH11/ADC2_CH0/FSPID/FSPIIO5/S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), U3.22 (WH)
W_HIGHSIDE_GATE: R28.1, U3.37 (HSW)
W_LOWSIDE: H1.19, U1.18 (GPIO10/TOUCH10/ADC1_CH9/FSPICS0/FSPIIO4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), U3.23 (WL)
W_LOWSIDE_GATE: R25.1, U3.3 (LSW)
W/PWM_ENCODER: R1.2, TP13.1, U2.8 (W/PWM)

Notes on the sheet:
ESP32 3.3V Power Filter
Fault LED's
5V_USB/5V -> 3.3V + PWR LED
Other
U PHASE MOSFETS
ESP & DRIVER CHIP
Tie low for standalone control, high for SPI controlled
PIN CONNECTOR
Chip Select (Active Low)
ESP INPUT
RESET BUTTON & PWR ON RESET
DRIVER POWER FILTER
BOOT BUTTON
Current Sense Pins
CURRENT SENSE OFFSET
DRIVER DEFAULT STATE PULL DOWN
BATTERY POWER
The wondering resistor (Can't be bothered to updated BOM to remove this)
LIPO PROTECTION (SOFTWARE)
W PHASE MOSFETS
ENCODER PADS OUT
USB C 16 Pin Connector
Tie to ground for internal clock
Voltage Divider to ESP32 Safe upto 36.3v 16.8v -> 1.527v 14.0v -> 1.273v
ENCODER BREAKOFF BOARD
BUCK CONVERTER LIPO -> 5v
V PHASE MOSFETS
STATUS LED's
ESP32 ESD Protection
LOW ESR ceramic Recommended

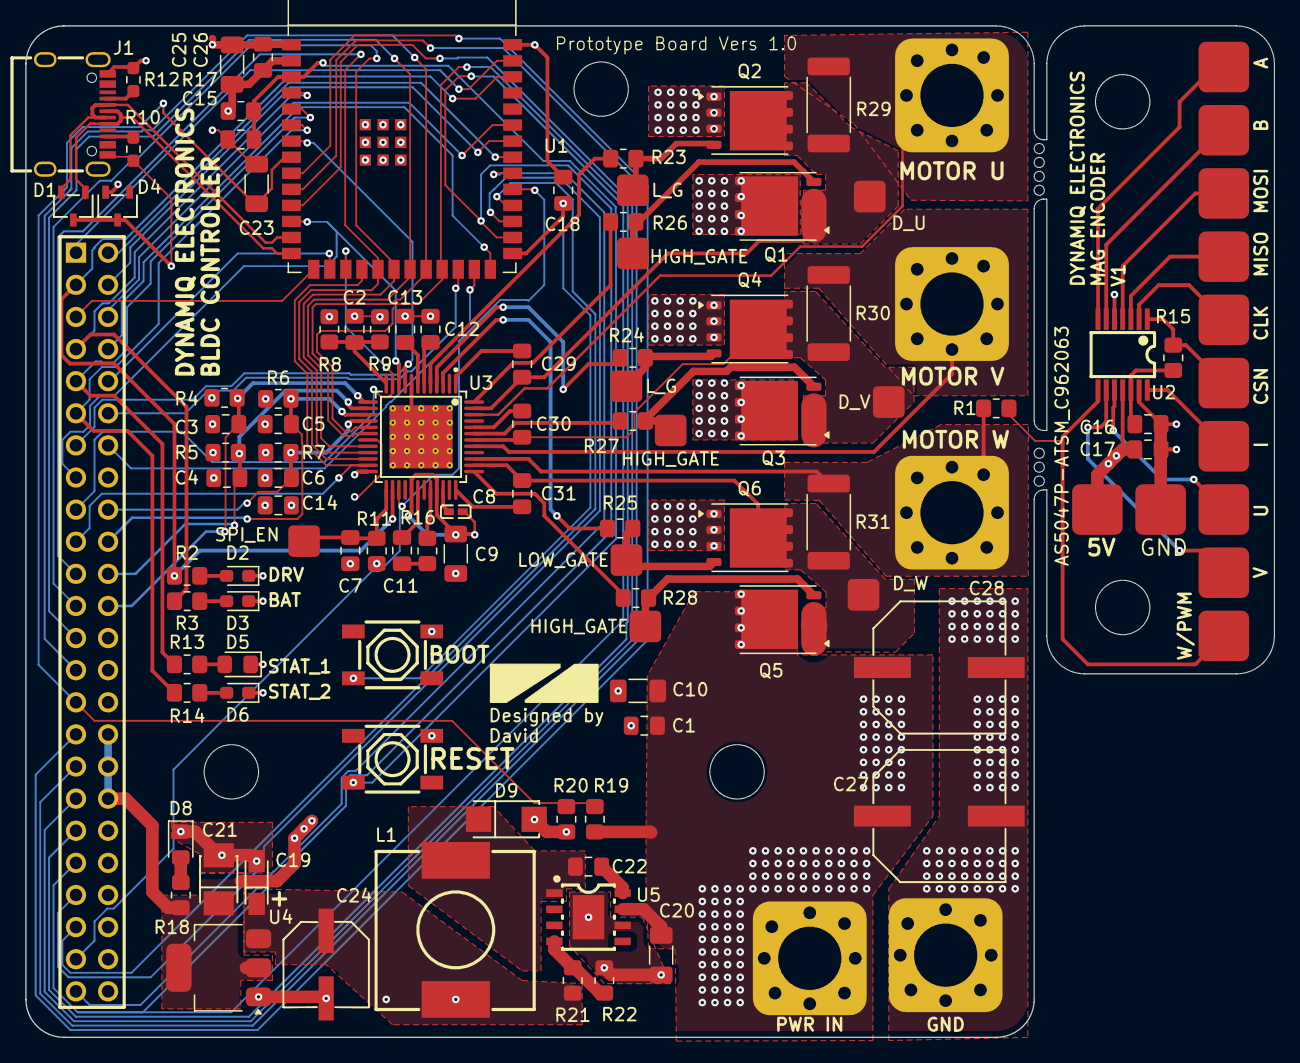
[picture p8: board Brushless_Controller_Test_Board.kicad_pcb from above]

Board: 4 copper layers, 98.8 x 80.0 mm, 113 parts (0 on the bottom side), 95 nets.

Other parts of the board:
GND: BAT_GND; PWR_THRU_HOLE
MOTOR U: Motor_Phase_U; PWR_THRU_HOLE
MOTOR V: Motor_Phase_V; PWR_THRU_HOLE
MOTOR W: Motor_Phase_W; PWR_THRU_HOLE
PWR IN: BAT_IN; PWR_THRU_HOLE

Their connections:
DRIVER_ANALOG_SUPPLY: PWR IN.1; also elsewhere on the board
GND: GND.1; also elsewhere on the board
MOTOR_U: MOTOR U.1; also elsewhere on the board
MOTOR_V: MOTOR V.1; also elsewhere on the board
MOTOR_W: MOTOR W.1; also elsewhere on the board

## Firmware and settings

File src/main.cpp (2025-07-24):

//////// Written by David J ////////
/////// ESP-32-S3 Wroom 1 Based BLDC Controller /////

/*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
    This program is distributed in the hope that it will be useful,
    but WITHOUT ANY WARRANTY; without even the implied warranty of
    MERCHANTABILITY or FITNESS FOR A PARTICULAR PURPOSE.  See the
    GNU General Public License for more details.
*/

#include <stdlib.h>

#include "math.h"

#include "esp32-hal-ledc.h"
#include "esp32-hal-cpu.h"
#include "esp_attr.h"

#include "soc/rtc.h"
#include "driver/mcpwm.h"
#include "soc/mcpwm_periph.h"

#include "../include/MotorController.h"
#include "../include/SerialManager.h"

// Include the library for the AS5047P sensor.
#include <AS5047P.h>

// Other Constants
#define CPU_FREQ_MHZ 160

#define PWM_FREQ 16384
#define PWM_RES 11

// define the spi bus speed for mag encoder
#define AS5047P_CUSTOM_SPI_BUS_SPEED 8000000 // 1Mhz

#define LIPO_DISABLE_VOLTAGE 14.0


// initialize a new AS5047P sensor object.
AS5047P magEncoder(ENCODER_CSN, AS5047P_CUSTOM_SPI_BUS_SPEED);

// init my motor drivers and serial manager
MotorController* m_motorController = new MotorController();
SerialManager* m_serialManager = new SerialManager();

bool disableSerialInput = false;

//////////////////////////////////////////////////////////////////////////////////////////////////////
//////////////////////////////////////////////////////////////////////////////////////////////////////

// Map double values
double mapf(double x, double in_min, double in_max, double out_min, double out_max) {
  return (x - in_min) * (out_max - out_min) / (in_max - in_min) + out_min;
}


// Returns the current voltage of the lipo battery
double getLipoVoltage() {
  // Voltage offset of lipo due to voltage divider tolerance
  const double LIPO_OFFSET = 0.7;
  return mapf(analogRead(LIPO_V_PIN), 0, 4095, 0, 36.3) + LIPO_OFFSET;
}


// Update stat LED's depending on the direction the motor is turning
double previousTheta = 0;
void updateLED(double currentTheta) {
  if (currentTheta > previousTheta) {
    // if theta is increasing then turn on stat 1
    digitalWrite(STAT_1_LED_PIN, HIGH);
    digitalWrite(STAT_2_LED_PIN, LOW);
  } else if (currentTheta < previousTheta) {
    // if theta is decreasing then turn on stat 2
    digitalWrite(STAT_1_LED_PIN, LOW);
    digitalWrite(STAT_2_LED_PIN, HIGH);
  } else {
    // if theta is stationary then turn on both
    digitalWrite(STAT_1_LED_PIN, HIGH);
    digitalWrite(STAT_2_LED_PIN, HIGH);
  }
  previousTheta = currentTheta;
}

void printArray(char* arr, int size) {
  for (int i = 0; i < size; i++) {
    Serial.println(arr[i]);
  }
}

double getPotValueMapped(double a, double b) {
  return mapf(analogRead(POT_PIN), 0, 4095.0, a, b);
}

double getSign(double num) {
  if (num == 0) return 0;
  if (num > 0) { return 1.0; } else { return -1.0; }
}

double clamp(double d, double min, double max) {
  const double t = d < min ? min : d;
  return t > max ? max : t;
}


void executeSerialCommand(SerialManager* serialManager) {
   // Print out command recieved
  SerialCommand userCommand = serialManager->readSerialCommand();
  if (userCommand.cmd == ' ') return;

  Serial.print("Command: ");
  Serial.print(userCommand.cmd);
  Serial.print(" Set to: ");
  Serial.println(userCommand.value, 5);

  // Process the command here
  switch (userCommand.cmd) {
    case 'b':
        Serial.print("Battery at ");
        Serial.println(getLipoVoltage());
        break;
    case 'e':
        Serial.println("Driver Enabled");
        m_motorController->setDriverEnable(true);
        break;
    case 'd':
        Serial.println("Driver Disabled");
        m_motorController->setIdle();
        break;
    case 'p':
        Serial.print("Position set to: ");
        Serial.println(userCommand.value, 5);
        m_motorController->setClosedLoopPosition(userCommand.value);
        break;
    case 't':
         *m_motorController->getTestValue() = userCommand.value;
        break;
    case 'o':
        Serial.println("Percentage Output Mode Enabled");
        m_motorController->openLoopPercentageOutput(userCommand.value);
        break;
    case 'l':
        Serial.println("Percentage Output Mode Enabled");
        m_motorController->closedLoopPercentageOutput(userCommand.value);
        break;
    case 'z':
        Serial.println("Serial Input Disabled...");
        disableSerialInput = true;
        break;
    default: // optional
        Serial.println("No matching cmd");
  }
}

//////////////////////////////////////////////////////////////////////////////////////////////////////
//////////////////////////////////////////////////////////////////////////////////////////////////////

void setup() {
  // Set CPU Freq
  setCpuFrequencyMhz(CPU_FREQ_MHZ);
  
  // Setup Driver Pins for the motor controller
  m_motorController->init();

  // Start serial communication
  m_serialManager->init();

  // Get the ESP32 to set the correct pins for encoder SPI (using its built in MUX)
  SPI.begin(ENCODER_CLK, ENCODER_MISO, ENCODER_MOSI, ENCODER_CSN);

  // Initialise the magnetic encoder
  while (!magEncoder.initSPI()) {
    Serial.println(F("Can't connect to the AS5047P sensor! Please check the connection..."));
    delay(5000);
  }
  delay(100);
}


bool lipoThresholdHit = false;
void loop() {
  m_motorController->update(magEncoder.readAngleDegree());
  if (!disableSerialInput) {
    m_serialManager->updateSerialInput();
  }
  executeSerialCommand(m_serialManager);

  // Lipo protection if statement
  if (getLipoVoltage() < LIPO_DISABLE_VOLTAGE || lipoThresholdHit) {
    lipoThresholdHit = true;
    digitalWrite(LIPO_LED_PIN, HIGH);
    m_motorController->setDriverEnable(false);
    m_motorController->setIdle();
    Serial.println("Lipo Voltage Threshold hit");
  }
}

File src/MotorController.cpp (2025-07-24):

#include "../include/MotorController.h"

MotorController::MotorController() {

}

void MotorController::init() {
    // Driver enable pin
    pinMode(DRV_EN_PIN, OUTPUT);

    // LED Pins
    pinMode(LIPO_LED_PIN, OUTPUT);
    pinMode(STAT_1_LED_PIN, OUTPUT);
    pinMode(STAT_2_LED_PIN, OUTPUT);

    // Phase enable pins
    pinMode(U_LS_PIN, OUTPUT);
    pinMode(V_LS_PIN, OUTPUT);
    pinMode(W_LS_PIN, OUTPUT);

    // Phase current sensing pins
    pinMode(U_CUR_PIN, INPUT);
    pinMode(V_CUR_PIN, INPUT);
    pinMode(W_CUR_PIN, INPUT);

    // Lipo voltage sensing pin
    pinMode(LIPO_V_PIN, INPUT);

    // Potentiometer pin
    pinMode(POT_PIN, INPUT);

    // setup GPIO output for mcpwm
    mcpwm_gpio_init(MCPWM_UNIT_0, MCPWM0A, U_HS_PIN);
    mcpwm_gpio_init(MCPWM_UNIT_0, MCPWM0B, V_HS_PIN);
    mcpwm_gpio_init(MCPWM_UNIT_0, MCPWM1A, W_HS_PIN);

    mcpwm_config_t pwm_config;
    pwm_config.frequency = 19000;    //frequency = 50Hz, i.e. for every servo motor time period should be 20ms
    pwm_config.cmpr_a = 0;    //duty cycle of PWMxA = 0
    pwm_config.cmpr_b = 0;    //duty cycle of PWMxb = 0
    pwm_config.counter_mode = MCPWM_UP_COUNTER;
    pwm_config.duty_mode = MCPWM_DUTY_MODE_0;

    mcpwm_init(MCPWM_UNIT_0, MCPWM_TIMER_0, &pwm_config);    //Configure PWM0A & PWM0B with above settings
    mcpwm_init(MCPWM_UNIT_0, MCPWM_TIMER_1, &pwm_config);    //Configure PWM0A & PWM0B with above settings
    
    mcpwm_sync_config_t sync_config;
    sync_config.sync_sig = MCPWM_SELECT_TIMER0_SYNC; // Gets the sync signal from timer 0
    sync_config.timer_val = 999; // The phase offset between the timers (999 makes them most in sync)
    sync_config.count_direction = MCPWM_TIMER_DIRECTION_UP; // The counter should count up
    
    mcpwm_sync_configure(MCPWM_UNIT_0, MCPWM_TIMER_1, &sync_config);
    mcpwm_set_timer_sync_output(MCPWM_UNIT_0, MCPWM_TIMER_0, MCPWM_SWSYNC_SOURCE_TEZ); // Setup an sync signal from timer 0
}


void MotorController::setDriverEnable(bool enable) {
  if (enable) {
    // Enable Driver
    digitalWrite(DRV_EN_PIN, HIGH);
    // Enable Phases
    digitalWrite(U_LS_PIN, HIGH);
    digitalWrite(V_LS_PIN, HIGH);
    digitalWrite(W_LS_PIN, HIGH);
  } else {
    // disable Driver
    digitalWrite(DRV_EN_PIN, LOW);
    // disable Phases
    digitalWrite(U_LS_PIN, LOW);
    digitalWrite(V_LS_PIN, LOW);
    digitalWrite(W_LS_PIN, LOW);
  }
}

void MotorController::setPhasePercentOutput(double uDutyPercent, double vDutyPercent, double wDutyPercent) {
  const double SAFETY_MAX_DUTY = 31;
  // Driver protection, if it exceeds this duty cycle the driver doesnt like it and faults :(
  if (uDutyPercent >= SAFETY_MAX_DUTY || vDutyPercent >= SAFETY_MAX_DUTY || wDutyPercent >= SAFETY_MAX_DUTY) {
    Serial.println("MAX PHASE DUTY EXCEEDED");
    return;
  }

  // set Phase U
  mcpwm_set_duty(MCPWM_UNIT_0, MCPWM_TIMER_0, MCPWM_OPR_A, uDutyPercent);
  // set phase V
  mcpwm_set_duty(MCPWM_UNIT_0, MCPWM_TIMER_0, MCPWM_OPR_B, vDutyPercent);
  // set phase W
  mcpwm_set_duty(MCPWM_UNIT_0, MCPWM_TIMER_1, MCPWM_OPR_A, wDutyPercent);
}

void MotorController::openLoopPercentageOutput(double percentOutput) {
  if (percentOutput == 0) {
    setIdle();
    return;
  }
  m_currentControlMode = ControlMode::OPEN_LOOP_PERCENT_OUTPUT;
  m_percentageOutput = percentOutput;
}

void MotorController::closedLoopPercentageOutput(double percentOutput) {
  if (percentOutput == 0) {
    setIdle();
    return;
  }
  m_currentControlMode = ControlMode::CLOSED_LOOP_PERCENT_OUTPUT;
  m_percentageOutput = percentOutput;
}

void MotorController::setClosedLoopPosition(double position) {
  m_currentControlMode = ControlMode::CLOSED_LOOP_POSITION;
  m_targetPosition = position;
}


void MotorController::setIdle() {
  setDriverEnable(false);
  setPhasePercentOutput(0, 0, 0);
  m_currentControlMode = ControlMode::IDLE;
  m_percentageOutput = 0.0;
  m_electricalThetaStep = 0.0;
}

void MotorController::setOpenLoopPosition(double position, bool physicalShaftPos) {
  m_currentControlMode = ControlMode::OPEN_LOOP_ELECTRICAL_POSITION;
  if (physicalShaftPos) {
    m_targetElectricalPosition = position * (M_PI / 180.0) * (MAGNETIC_POLE_COUNTS / 2.0);
    return;
  }
  m_targetElectricalPosition = position;
}


// open loop svpwmCommutation
void MotorController::svpwmCommutation() {

  m_percentageOutput = clamp(m_percentageOutput, -100.0, 100.0);

  // Ramping so that the velocity doesnt change instantly causing high current spikes
  double targetElectricalThetaStep = mapf(m_percentageOutput, -100, 100, -0.1, 0.1);
  m_electricalThetaStep += (targetElectricalThetaStep - m_electricalThetaStep) * deltaElectricalThetaStep_KP;

  if (fabs(targetElectricalThetaStep - m_electricalThetaStep) < 0.01) {
    m_electricalThetaStep = targetElectricalThetaStep;
  }

  // sets the target electrical theta with a step added
  double targetElectricalTheta = m_electricalTheta + m_electricalThetaStep;

  // Find the trig ratio for the output between 0 - 100%
  double U_duty = sin(targetElectricalTheta) * 50.0 + 50.0;
  double V_duty = sin(targetElectricalTheta + 120.0 * M_PI / 180.0) * 50.0 + 50.0;
  double W_duty = sin(targetElectricalTheta + 240.0 * M_PI / 180.0) * 50.0 + 50.0;

  double MAX_TORQUE = 0.07 + 1.5 * fabs(m_electricalThetaStep); // limit the maximum duty percentage of the PWM (assumes linear relationship to keep the motor turning at high speed)

  // Set the phase with the output above
  setPhasePercentOutput(U_duty * MAX_TORQUE, V_duty * MAX_TORQUE, W_duty * MAX_TORQUE);

  // assumes the electrical theta is now at the target (hence open loop control)
  m_electricalTheta = targetElectricalTheta;
  
  // Serial.print(">CA:");
  // Serial.println(fmod((m_encoderAngle * MAGNETIC_POLE_COUNTS / 2.0) + 145, 360), 4);

  // Serial.print(">EA:");
  // Serial.println(fmod(m_electricalTheta * 180.0 / M_PI, 360.0), 4);
}
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

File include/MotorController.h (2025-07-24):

#include <Arduino.h>

#include "soc/rtc.h"
#include "driver/mcpwm.h"
#include "soc/mcpwm_periph.h"

// Pin definition
#define DRV_EN_PIN 38
// Low side control pins
#define W_LS_PIN 10
#define V_LS_PIN 12
#define U_LS_PIN 14

// High side control pins
#define U_HS_PIN 21
#define V_HS_PIN 13
#define W_HS_PIN 11

// Current sensing input
#define U_CUR_PIN 7
#define V_CUR_PIN 8
#define W_CUR_PIN 9

// Encoder SPI pins
#define ENCODER_CLK 39
#define ENCODER_MISO 40
#define ENCODER_MOSI 41
#define ENCODER_CSN 42

#define POT_PIN 18

// Lipo voltage
#define LIPO_V_PIN 15
// Lipo Error LED
#define LIPO_LED_PIN 4
// Status LED's
#define STAT_1_LED_PIN 5
#define STAT_2_LED_PIN 6

// Motor Magnet Pole Count
#define MAGNETIC_POLE_COUNTS 40

  enum ControlMode {
    IDLE,
    OPEN_LOOP_PERCENT_OUTPUT,
    OPEN_LOOP_ELECTRICAL_POSITION,
    CLOSED_LOOP_PERCENT_OUTPUT,
    CLOSED_LOOP_POSITION
  };

class MotorController {
  public:



    MotorController();
    void init(); // Sets up the board pins to the correct INPUT / OUTPUT
    void update(double encAngle); // this needs to be in the main loop for the motor to update and spin
    void setDriverEnable(bool enable);
    void setIdle(); // puts the driver into idle mode
    void openLoopPercentageOutput(double percentOutput); // uses SVPWM with no feedback loop from mag encoder
    void setOpenLoopPosition(double position, bool physicalShaftPos = false);
    void closedLoopPercentageOutput(double percentOutput); // Using encoder feedback to update the electrical theta
    void setClosedLoopPosition(double position);

    double* getTestValue() { return &testValue; }

  private: 
    void setPhasePercentOutput(double uDutyPercent, double vDutyPercent, double wDutyPercent);
    void svpwmCommutation();
    void svpwmEncoderCommutation();

    double mapf(double x, double in_min, double in_max, double out_min, double out_max) {
      return (x - in_min) * (out_max - out_min) / (in_max - in_min) + out_min;
    };
    double clamp(double d, double min, double max) {
      const double t = d < min ? min : d;
      return t > max ? max : t;
    }
    double getSign(double num) {
      if (num == 0) return 0;
      if (num > 0) { return 1.0; } else { return -1.0; }
    }

    
    ControlMode m_currentControlMode = ControlMode::IDLE;

    double m_electricalTheta = 0.0; // degrees for electrical theta state not physical
    double m_electricalThetaStep = 0.0; // This depicts how much the theta steps to rotate the motor

    double const deltaElectricalThetaStep_KP = 0.001; // KP values used for the acceleration of the motor

    double m_percentageOutput = 0.0; 

    // Used by OPEN_LOOP_ELECTRICAL_POSITION control mode
    double m_targetElectricalPosition = 0.0;

    // Used by CLOSED_LOOP_POSITION control mode
    double m_targetPosition = 0.0;

    double m_encoderAngle = 0.0;

    double m_torque = 0.0;

    // test value that can be adjusted in real time by serial
    double testValue = 145;
};

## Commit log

2025-07-20 Fixed ordering, code should now build
    [main.cpp]
2025-07-20 Build Fixes & Created classes for motor controller
    [MotorController.cpp, MotorController.h, SerialManager.cpp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]
2025-07-22 Using teleplot and changed encoder speed
2025-07-24 PCB Files uploaded
    [Brushless Breakout Board BOM.xlsx, Brushless_Controller_Test_Board.kicad_pcb, Brushless_Controller_Test_Board.kicad_sch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]
2025-07-31 Most of the schematic is completed
    [BLDC_Version1_1_0.kicad_pcb, BLDC_Version1_1_0.kicad_sch, Gate Driver.kicad_sch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]
2025-08-02 Added pins
    [BLDC_Version1_1_0.kicad_sch, MosfetGates.kicad_sch, Power.kicad_sch]
2025-08-05 Added soft starter to PCB
    [BLDC_Version1_1_0.kicad_sch, MosfetGates.kicad_sch, Power.kicad_sch]
2025-08-09 Added ESD protection and test pins
    [BLDC_Version1_1_0.kicad_sch, Connectors.kicad_sch, Gate Driver.kicad_sch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]
2025-08-10 began part placement
    [BLDC_Version1_1_0.kicad_pcb, BLDC_Version1_1_0.kicad_sch, Connectors.kicad_sch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]
2025-08-11 Completed Placement of Parts
    [BLDC_Version1_1_0.kicad_pcb, Connectors.kicad_sch, Gate Driver.kicad_sch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]
2025-08-12 began working on the routing
    [BLDC_Version1_1_0.kicad_pcb, Connectors.kicad_sch, MosfetGates.kicad_sch]
2025-08-13 worked on traces
    [BLDC_Version1_1_0.kicad_pcb]
2025-08-14 Routing Complete
    [BLDC_Version1_1_0.kicad_pcb]
2025-08-14 Added silkscreen texts and logo
    [BLDC_Version1_1_0.kicad_pcb, BLDC_Version1_1_0.kicad_sch, MosfetGates.kicad_sch]
2025-08-19 Minor changes
    [BLDC_Version1_1_0-CuBottom.gbr, BLDC_Version1_1_0-CuIn1.gbr, BLDC_Version1_1_0-CuIn2.gbr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]

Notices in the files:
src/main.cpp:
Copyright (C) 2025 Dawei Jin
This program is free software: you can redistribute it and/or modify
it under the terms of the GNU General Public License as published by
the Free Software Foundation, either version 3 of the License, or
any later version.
